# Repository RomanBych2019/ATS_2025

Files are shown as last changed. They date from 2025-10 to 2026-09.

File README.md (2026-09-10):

# ATS

Проект тарировочной станции на основе контроллера ESP32.
Дисплей на базе Nextion 5'.

# Основные возможности

Работа с ДУТами с интерфейсами:
- Аналоговый, напряжение
- Аналоговый, частота
- RS485, протокол LLS
- BLE фирмы Эскорт

Работа в режимах:
- Счетчик - подсчет топлива, прошедшего через счетчик. Запоминание промежуточных значений, управление насосом.
- Выдача топлива - выдача введенного объема топлива.
- Автоматическое выкачивание - выкачивание топлива из бака до тех пор, пока скорость потока не станет менее 5 л/мин.
- Калибровка счетчика - вычисление количества импульсов для калибровки счетчика.
- Тарировка бака - тарировка бака порциями топлива.

Станция передает данные в терминал спутникового мониторинга, подключенный по RS485 (19200, 8, 1), протокол передачи Modbus RTU.
Станция записывает лог работы во внутреннюю flash-память.

# Сборка

Проект собирается через PlatformIO. В `platformio.ini` есть два варианта прошивки:

- `esp32dev` - основная сборка без Web Portal и Wi-Fi.
- `esp32dev_web` - сборка с Web Portal, Wi-Fi и OTA через флаг `ENABLE_WEB_PORTAL`.

Команды сборки:

```sh
pio run -e esp32dev
pio run -e esp32dev_web
```

В обычной сборке `WebUi.cpp`, `WifiManager.cpp` и зависимость `GyverPortal` не используются. В web-сборке они подключаются на этапе выбора environment.

# Web Portal

Web Portal доступен только в сборке `esp32dev_web`.

Станция работает в режиме точки доступа:
- SSID: `WiFi ATS`
- Пароль: `00000001`

Страницы:
- `192.168.4.1` - управление станцией и доступ к логу.
- `192.168.4.1/ota_update` - загрузка новой прошивки.

# Структура

Крупные части логики вынесены из `main.cpp` в отдельные модули:
- `HmiRenderer` - рендеринг экранов Nextion.
- `WebUi` - страницы и обработчики Web Portal.
- `WifiManager` - настройка Wi-Fi и login portal.
- `ModbusTable` - таблица Modbus и обновление регистров.

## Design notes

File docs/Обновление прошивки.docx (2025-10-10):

1. Подключиться к Wi-Fi сети ATC, paswd: 12_04_19
2. Убедиться, что присвоен IP адрес из диапазона 192.168.4.ххх
3. Перейти в браузере по адресу 192.168.4.1/upgrade

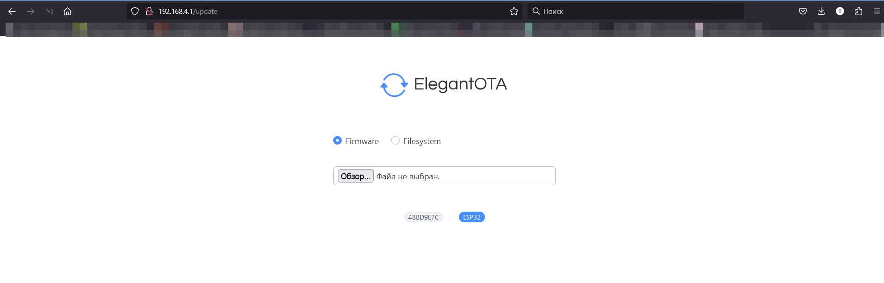
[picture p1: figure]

4. Выбрать файл для загрузки firmware.bin нажатием кнопки Обзор
5. Дождаться окончания загрузки

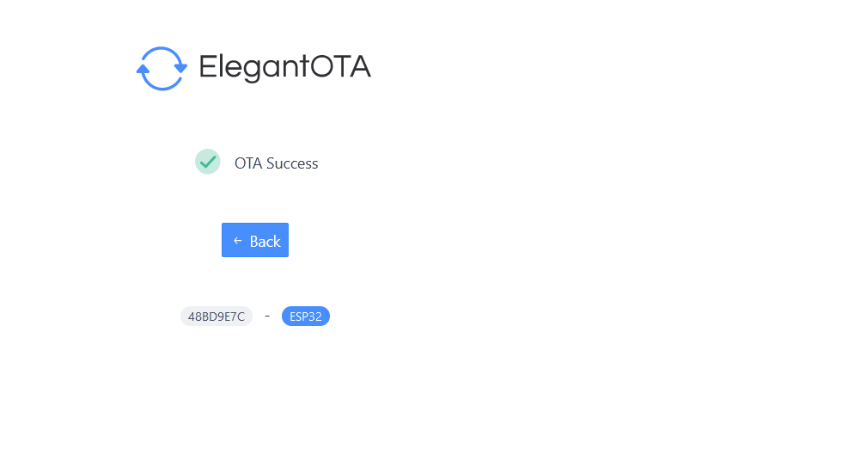
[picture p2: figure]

6. Все! Прошивка обновлена. Проверить можно вновь подключившись к Wi-Fi сети ATC и зайдя на адрес 192.168.4.1

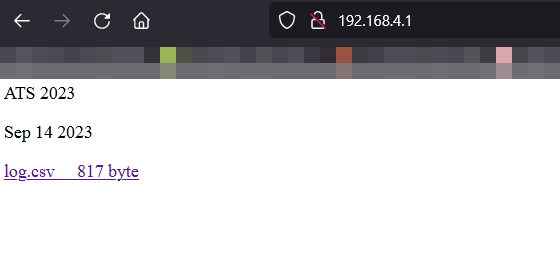
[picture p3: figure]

Скачав файл log.svc можно получить историю тарировок с датами начала, идентификатором и настройками каждой тарировки.

Удаление файла из памяти станции по ссылке http://192.168.4.1/delete

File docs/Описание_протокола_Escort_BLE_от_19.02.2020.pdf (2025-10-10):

2020

## УТВЕРЖДЕНО А.В.00001-01 33 01-ЛУ

## ПРОТОКОЛ ВЗАИМОДЕЙСТВИЯ УСТРОЙСТВ НА БЕСПРОВОДНОЙ ТЕХНОЛОГИИ С НИЗКИМ ЭЛЕКТРОПОТРЕБЛЕНИЕМ (ЭСКОРТ.BLE)

## Руководство программиста

А.В.00001-01 33 01

А.В.00001-01 33 01

## АННОТАЦИЯ

### В данном программном документе приведено руководство программиста по использованию протокола взаимодействия устройств на беспроводной технологии с

низким электропотреблением ЭСКОРТ.BLE.

В данном программном документе, в разделе «Термины, определения, обозначения и сокращения» описаны используемые в описании протокола термины,

### определения, обозначения и сокращения для однозначной трактовки в рамках данного

протокола.

### В разделе «Параметры соединения» приведено описание параметров необходимых для установления соединения между управляющим и оконечным

устройством.

### В данном программном документе, в разделе «Структура сообщения» приведено описание организации обмена данными между управляющим и оконечным

устройством.

### В разделе «Передаваемые параметры» описана структура используемых в организации обмена данными между управляющим и оконечным устройством

параметров и приведен список используемых параметров.

### В данном программном документе, в разделе «Используемые команды» приведено описание команд обеспечивающих выполнение тех или иных действий по

запросу от управляющего устройства оконечным устройством.

Оформление | программного | документа | «Руководство | программиста»

### произведено по требованиям ЕСПД (ГОСТ 19.101-7

### 1), ГОСТ 19.103-77²⁾, ГОСТ 19.104-

78*³⁾, ГОСТ 19.105-78*⁴⁾, ГОСТ 19.106-78*⁵⁾, ГОСТ 19.504-79*⁶⁾, ГОСТ 19.604-78*⁷⁾).

1) ГОСТ 19.101-77 ЕСПД. Виды программ и программных документов
2) ГОСТ 19.103-77 ЕСПД. Обозначение программ и программных документов
3) ГОСТ 19.104-78* ЕСПД. Основные надписи
4) ГОСТ 19.105-78* ЕСПД. Общие требования к программным документам
5) ГОСТ 19.106-78* ЕСПД. Общие требования к программным документам, выполненным печатным способом
6) ГОСТ 19.504-79* ЕСПД. Руководство программиста. Требования к содержанию и оформлению
7) ГОСТ 19.604-78* ЕСПД. Правила внесения изменений в программные документы, выполненные печатным способом

### Оглавление

3.1. РЕЖИМ НЕПОСРЕДСТВЕННОГО СОЕДИНЕНИЯ С СЕРВИСОМ УСТРОЙСТВА........7
4.1. РЕЖИМ НЕПОСРЕДСТВЕННОГО СОЕДИНЕНИЯ С СЕРВИСОМ УСТРОЙСТВА........8

### 1. ТЕРМИНЫ, ОПРЕДЕЛЕНИЯ, ОБОЗНАЧЕНИЯ И СОКРАЩЕНИЯ

В данном протоколе применены следующие термины с соответствующими определениями:

* | Управляющее устройство — устройство осуществляющее формирование команд управления (в дальнейшем запросов) и прием ответных команд (в дальнейшем ответов).
* | Оконечное устройство — устройство преобразующее физические воздействия в параметры и отвечающее на команды управления.
* | Команда — набор букв, означающий необходимость выполнения того или иного действия.
* | Параметр команды — конструкция, позволяющая идентифицировать и передать некоторое значение.
* | Разделитель полей — символ, разделяющий команды и параметры.
* | Разделитель параметра — символ, отделяющий элементы параметра.
* | Исходящие параметры — параметры, передаваемые из управляющего устройства в оконечное.
* | Входящие параметры — параметры, передаваемые из оконечного устройства в управляющее.
* | Характеристика (Characteristic) — это значение передаваемых данных, используемое в сервисе, а также информация конфигурации о том, как осуществляется доступ к этому значению, и информация о том, как это значение отображается.
* | Сервис (Service) — это набор характеристик, сервис представляет собой набор данных и связанных с ними действий для выполнения определенной функции или задачи.
* | Универсальный уникальный идентификатор (Universally Unique ID) - это уникальный номер, используемый для идентификации служб, характеристик и дескрипторов, также называемых атрибутами.
* | Advertising — процесс широковещательной трансляции пакетов оконечным BLE устройством. В этих пакетах оконечное устройство сообщает своё имя и адрес, сообщает о сервисах, которые предоставляет, а также специальную информацию.
* | Manufacturer specific data – поле в advertising сообщении, в котором широковещательно передаются измеряемые параметры оконечным устройством.

В данном протоколе применены следующие обозначения и сокращения:

UUID - (Universally Unique ID) Универсальный уникальный идентификатор;
BLE - (Bluetooth Low Energy) технология Bluetooth c низким энергопотреблением.

### 2. ПАРАМЕТРЫ СОЕДИНЕНИЯ

На физическом уровне соединение с оконечным устройством реализовано на основе стандарта Bluetooth 4.0 со следующими параметрами соединения :
Параметр | Значение
advertising_interval | 1000 мс
connection_interval | 900 мс
slave_latency | 1
conn_sup_timeout | 5000 мс

Оконечные устройства имеют уникальное имя в формате TD_XXXXXX –для топливного датчика , TL_XXXXXX-для датчика температуры и освещенности , TT_XXXXXX- для датчика температуры ,TH_XXXXXX- для датчика температуры влажности ,давления и освещенности , DU_XXXXXX для датчика угла наклона , где XXXXXX - представляет собой серийный номер оконечного устройства.
С оконечными устройствами можно взаимодействовать двумя способами: при помощи непосредственного соединения с устройством и обменом данными при помощи характеристик Rx characteristics и Tx characteristics UUID (двухсторонний обмен – наиболее подходит для начальной
настройки | (калибровки) устройства), | либо при | помощи | advertising | (рекламных | либо
широковещательных) пакетов, что обеспечивает лишь односторонний обмен с оконечным устройством – получение телеметрических данных измеряемых оконечным устройством.
Оба этих режима работают независимо, то есть при установлении непосредственного соединения с каким-либо управляющим устройством оконечное устройство не перестает рассылать advertising сообщения.

### 2.1. Режим непосредственного соединения (рекомендуется для конфигурации оконечного

устройства)

Обмен происходит при помощи BLE -сервиса включающего две характеристики:

2.1.1. Service UUID: 6E400001-B5A3-F393-E0A9-XXXXXXXXXXXX (little endian) - идентификатор сервиса при помощи которого осуществляется обмен данными между управляющим и оконечным устройством.
Передача данных от управляющего к оконечному устройству осуществляется путем записи в идентификатор характеристики для передачи данных управляющим устройством (Tx characteristics UUID).
Прием данных от оконечного устройства осуществляется путем считывания идентификатора характеристики для приема данных управляющим устройством (Rx characteristics UUID)
2.1.2. Rx characteristics UUID: 6E400003-B5A3-F393-E0A9-XXXXXXXXXXXX (little endian) -идентификатор характеристики для приёма данных управляющим устройством.
2.1.3. Tx characteristics UUID: 6E400002-B5A3-F393-E0A9-XXXXXXXXXXXX (little endian) -идентификатор характеристики для передачи данных управляющим устройством.

Примечание:
XXXXXXXXXXXX это уникальная часть UUID для каждой пары (управляющее-оконечное) устройство.

### 2.2. Режим связи через advertising (широковещательные) пакеты

Оконечное устройство отсылает через равные промежутки времени (1000 ms) advertising пакеты и передает в поле manufacturer specific data данные телеметрии уникальные для каждого типа оконечного устройства.
В режиме когда к датчику нет непосредственного соединения, advertising ведется в режиме Connectable undirected (ненаправленное, с возможностью соединения). При наличии соединения с сервисом оконечного устройства (непосредственное соединение) advertising ведется в режиме Non connectable undirected (ненаправленное без возможности соединения).

Пример пакетов advertising:
1. Non connectable undirected (ненаправленное, без возможности соединения) 0x0201060FFF160F01B50B1D1875CF1D000000800A0954445F313030303032.
2. Connectable undirected (ненаправленное, с возможностью соединения) 0x0201060FFF160F01B50B1D1875CF1D000000800A0954445F3130303030321107A286C1DDEEFFA9 E093F3A3B50100406E.

Разбор advertising пакета:
1. 020106
Длина = 0x02, Тип 0x01 = «Flags»
Данные = 06, что соответствует BLE_GAP_ADV_FLAG_LE_GENERAL_DISC_MODE BLE_GAP_ADV_FLAG_BR_EDR_NOT_SUPPORTED
2. 0FFF160F01CF0B1D1775CF1D00000080
Длина = 0x0F, Тип 0xFF = «Manufacturer data»
Данные = 160F01CF0B1D1775CF1D00000080 - это полезные данные, предаваемые датчиком, разбор и формат этих данных приведен в параграфе 3. СТРУКТУРА СООБЩЕНИЯ и 4.ПЕРЕДАВАЕМЫЕ ПАРАМЕТРЫ
3. 0A0954445F313030303032
Длина = 0x0A, Тип 0x09 = «Complete Local Name» (имя устройства) Данные = 54445F313030303032 =TD_100002 (hex –ascii)
4. 1107A286C1DDEEFFA9E093F3A3B50100406E
Длина = 0x11, Тип 0x07 = «Complete List of 128-bit Service Class UUIDs» Данные = A286C1DDEEFFA9E093F3A3B50100406E

### 3. СТРУКТУРА СООБЩЕНИЯ

### 3.1. Режим непосредственного соединения с сервисом устройства

В режиме непосредственного соединения все сообщения передаются в виде следующей структуры:

Тип поля | Пример
Команда / Ответ на команду | Например, SP –установить пароль Ответом на команду будет (в случае успеха) APO или APE (в случае неудачи) Подробнее о командах в параграфе 5.
разделитель полей | запятая
параметр1 | PW:1:123456 –старый пароль , необходим для установки нового Подробнее о параметрах в параграфе 4.
разделитель полей | запятая
параметр2 (если необходимо) | PN:1:5555 –новый пароль. Подробнее о параметрах в параграфе 4.
разделитель полей | запятая
конец сообщения | символ конца строки (\r)

Итоговое сообщение:

SP,PW:1:123456,PN:1:5555\r –установить новый пароль 5555, при условии что старый пароль был 123456.

Примечания:
1. Сообщение может быть без параметров. В этом случае разделители полей отсутствуют.
2. Количество параметров в сообщении может быть произвольным (рекомендуется не более 20).

### 3.2. Поле manufacturer data в advertising сообщении

Все параметры передаются в поле manufacturer data и имеют фиксированный размер в байтах. Первые два байта в поле manufacturer data задают параметр company id.
Следующий байт задает параметр hardware id –тип устройства с которым ведется работа
В зависимости от hardware id изменяется формат дальнейших данных, который является уникальным для каждого типа устройств.
Формат передаваемых данных и пример посылок приведен в параграфе 4.2 ПЕРЕДАВАЕМЫЕ ПАРАМЕТРЫ.

### 4. ПЕРЕДАВАЕМЫЕ ПАРАМЕТРЫ

### 4.1. Режим непосредственного соединения с сервисом устройства

4.1.1. Структура передаваемого параметра

Передаваемый параметр представляет собой конструкцию ИМЯ: ТИП: ЗНАЧЕНИЕ.

ИМЯ –символьное название параметра. (см. табл.1, табл.2, табл.3)
РАЗДЕЛИТЕЛЬ ПАРАМЕТРА — двоеточие.
ТИП – тип передаваемого параметра,
0 - ЧИСЛО ШЕСТНАДЦАТЕРИЧНОГО ФОРМАТА (HEX) ЗАПИСАННОЕ В КОДЕ ASCII
1 – ЦЕЛОЧИСЛЕННЫЙ (РЕКОМЕНДУЕТСЯ ИСПОЛЬЗОВАТЬ INT_16)
2 – С ПЛАВАЮЩЕЙ ТОЧКОЙ (РЕКОМЕНДУЕТСЯ FLOAT),
3 – СТРОКОВЫЙ (ПРОИЗВОЛЬНАЯ СТРОКА - РЕКОМЕНДУЕТСЯ НЕ БОЛЕЕ 12 СИМВОЛОВ) РАЗДЕЛИТЕЛЬ ПАРАМЕТРА — двоеточие.
ЗНАЧЕНИЕ – значение в зависимости от типа.

Пример ответа на команду GD\r «Выдать динамические параметры»: AGD,UT:1:-20,UL:1:1024,VB:2:3.62,ER:3:overcool\r

Входящие параметры в строке:
* | Температура = -20 град.
* | Уровень = 1024 у.е.
* | Напряжение батареи = 3,62 В.
* | За время между сеансами связи оконечного устройства с управляющим произошла ошибка overcool— переохлаждение.

Примечания:

1. Количество передаваемых параметров определяется разработчиком прибора в зависимости от его специфики и режима работы. Количество параметров в сообщении может быть произвольным (рекомендуется не более 20) при указанных рекомендуемых параметрах размер буфера на приеме и передаче не должен превышать 512 байт.
2. Если не указано иного тип параметра считать целочисленным.
3. Опционально при выполнении запроса могут быть добавлены параметры вида N1, N2, N3…….
4. Порядок следования параметров может быть произвольным, некоторые параметры могут отсутствовать.

4.1.2. Список рекомендуемых динамических параметров приведен в таблице 1. Таблица 1. Список рекомендуемых динамических параметров
Параметр | Величина | Примечание
UT | Значение температуры | В градусах Цельсия
UL | Значение уровня для топливного датчика (событие сработки для датчика угла) | В диапазоне 0...4095 или 0..1023 в зависимости от режима для топливного датчика В диапазоне от 0..2 для датчика угла
UM | Значение уровня | В мм.
UZ | Накопленный измеренный расход | В литрах ***
UC | Счетчик событий (импульсов) | В событиях***
US | Измеренный период сигнала | В ms
UV | Измеренное напряжение | В вольтах
UI | Измеренный ток | В амперах
UF | Измеренная частота | В Гц.
UP | Измеренное давление | В паскалях
UM | Измеренный вес | В кг.
UN | Угол наклона | в градусах
UA | Азимут | В градусах
QV | Уровень вибрации (качество вождения) | В баллах больше-хуже
DC | Битовая маска сухого контакта | Не более 15 контактов.
VB | Напряжение питания (батареи)
ER | Ошибка, возникшая в процессе работы
TO | Время включения (в режиме отвал) ,Время накопления данных угла (в режиме ковш) | В секундах , не более 200 секунд
TF | Время выключения(в режиме отвал и ковш) | В секундах , не более 200 секунд

Примечание:
*** Счетчик. Сбрасывается соответствующей командой сброса

4.1.3. Список рекомендуемых калибровочных параметров приведен в таблице 2.

Таблица 2. Список рекомендуемых калибровочных параметров

HK | Верхнее калибровочное значение параметра
LK | Нижнее калибровочное значение параметра
AK | Зафиксировать горизонтальное положение
AС | Значение коэффициента 2 порядка при аппроксимации параметра
AB | Значение коэффициента 1 порядка при аппроксимации параметра
AА | Значение постоянной составляющей при аппроксимации параметра
AD | Значение коэффициента 3 порядка при аппроксимации параметра
PW | Пароль на смену калибровочных значений
PN | Новый пароль при смене пароля
WM | Режим работы | Определяется разработчиком.
UD | UUID
4.1.4. Список рекомендуемых статических параметров приведен в таблице 3.

Таблица 3. Список рекомендуемых статических параметров

SE | Серийный номер прибора.
VV | Версия прошивки
VD | Тип устройства.
CR | Контрольная сумма прошивки. | CRC32 вычисляется в момент формирования значения параметра.
FP | Ввод заводского пароля. | Для программирования параметров исключительно в процессе производства.

### 4.2. Поле manufacturer data в advertising сообщении

Общая структура поля Manufacturer data в advertising сообщении (справедлива для всех типов оконечных устройств).

Номер байта | 0 | 1 | 2 | 3 | 4 и далее
Значение | Длина поля | Тип поля (Manufacturer data) | Company ID | Hardware id (тип устройства) | Полезные данные (параметры датчика)
Пример | 0x0F | Всегда 0xFF | 0x0F16 | 0x01- ДУТ | 0xCF0B1D1775CF1D00000080

Для того чтобы различать типы устройств был введен байт hardware id -тип устройства, список устройств приведен ниже. Байт hardware id определяет набор полезных параметров получаемых от оконечного устройства их размер и порядок следования.

Байт hardware id | Тип устройства
0x01 | Датчик уровня топлива (ДУТ)
0x02 | Температурный датчик
0x03 | Температурный датчик c измерением уровня освещенности
0x04 | Датчик угла
0x05 | Датчик температуры, влажности, освещённости и давления

Список устройств может быть расширен.
Ниже приводится формат посылки полезных параметров для каждого из типов устройств.

Датчик уровня топлива (ДУТ), 0x01 - тип устройства. Имя вида TD_XXXXXX ,где XXXXXX соответствует серийному номеру.

Номер по порядку | Тип параметра | Длина параметра (байт) | Диапазон | Единица измерения | Пример
1 | Уровень топлива | 2 | 0...1023 или 0…4095 | Условные единицы | 2C0C - уровень (обратный порядок байт) 0с2с (hex) = 3116 (dec)
2 | Напряжение встроенной батареи | 1 | 2..4 | Вольт*10 | 1D - напряжение батареи *10 = 29 (dec)= 2.9 вольта
3 | Температура | 1 | -70..125 | Градус Цельсия | 17- темпрература = 23 (dec) градуса
4 | Версия прошивки | 1 | 0..255 | Номер версии | 74 -версия прошивки = 116 (dec)
5 | Период (непосредствен но измеренный параметр) | 4 | 0..500000 | Условные единицы | CF1D0000 (обратный порядок байт) =00001DCF(hex)= 7631(dec)
6 | Режим работы (определяет в каком диапазоне | 1 | Два значения: 0x80- 4095 0x00 -1024 | Нет | Если установлен диапазон 4095, байт принимает значение 0x80 , если 1024 ,то 0x00

| работает датчик)
7 | Сглаживание (младший полубайт) + Термокомпенса ция(старший полубайт) | 1 | Сглаживание : 0x0..0xF (0..15) Термокомпенса ция: Два значения: 0x8-выключена 0x0 -включена | Условные единицы | 0x81 Термокомпенсация выключена , Сглаживание=0x1(hex)= 1(dec) 0x0F Термокомпенсация включена , Сглаживание=0xF(hex)= 15(dec)

Температурный датчик ,0x02 - тип устройства. Имя вида TT_XXXXXX ,где XXXXXX соответствует серийному номеру.

Номер по порядку | Тип параметра | Длина параметра (байт) | Диапазон | Единица измерения | Пример
1 | Температура | 2 | -700..1250 | Градус Цельсия*10 | 6E01 - температура*10 (обратный порядок байт) - 016E (hex) = 366 (dec) =36.6 градусов
2 | Напряжение встроенной батареи | 1 | 2..4 | Вольт*10 | 1D - напряжение батареи *10 = 29 (dec)= 2.9 вольта
3 | Версия прошивки | 1 | 0..255 | Номер версии | 7C -версия прошивки = 124 (dec)

Температурный датчик c измерением уровня освещенности ,0x03 - тип устройства. Имя вида TL_XXXXXX, где XXXXXX соответствует серийному номеру.

Номер по порядку | Тип параметра | Длина параметра (байт) | Диапазон | Единица измерения | Пример
1 | Температура | 2 | -700...1250 | Градус Цельсия*10 | 6E01 - температура*10 (обратный порядок байт) - 016E (hex) = 366 (dec) =36.6 градусов
2 | Освещённость | 2 | 0...10000 | Люкс | Освещенность (обратный порядок байт) - 0с2с (hex) = 3116 (dec) =3116 люкс
3 | Напряжение встроенной батареи | 1 | 2...4 | Вольт*10 | 1D - напряжение батареи *10 = 29 (dec)= 2.9 вольта

4 | Версия
прошивки
1 | 0...255 | Номер версии

7D -версия прошивки =
125 (dec)

Датчик угла,0x04 - тип устройства . Имя устройства вида DU_XXXXXX ,где XXXXXX соответствует серийному номеру.

Номер по порядку | Тип параметра | Длина параметра (байт) | Диапазон | Единица измерения | Пример
1 | Режим датчика угла | 1 | 0,4,5,6,9,10 | Режим, подробнее в паспорте на DU-BLE , и в руководстве | 0x06=Режим 6= Включен режим датчика угла
2 | Событие сработки | 1 | 0..2 | Событие сработки подробнее в паспорте на DU-BLE , и в руководстве | В режиме 6 : 0x01-произошло событие сработки- угол превышен
3 | Угол наклона | 2 | 0..180 | Градус | 0x0300 (little endian)-обратный порядок байт =3(dec) градуса
4 | Температура | 1 | -70...125 | Градус Цельсия | 0x17(hex)- температура = 23 (dec) градуса , параметр не используется в 102 версии прошивки , передается всегда 0x00
5 | Верхняя калибровка угла | 2 | 0...180 | Градус, подробнее в паспорте на DU-BLE , и в руководстве | 0x0096 (big endian) =225 (dec) градусов
6 | Нижняя калибровка угла | 2 | 0...180 | Градус, подробнее в паспорте на DU-BLE , и в руководстве | 0x0005 (big endian) =5 (dec) градусов

7 | Напряжение встроенной батареи | 1 | 2...4 | Вольт*10 | 0x1D(hex) - напряжение батареи *10 = 29 (dec)= 2.9 вольта
8 | Версия прошивки | 1 | 0...255 | Номер версии | 0x66(hex) -версия прошивки = 102 (dec)

Датчик температуры, влажности, освещённости и давления,0x05 - тип устройства. Имя вида TH_XXXXXX ,где XXXXXX соответствует серийному номеру.

Номер по порядку | Тип параметра | Длина параметра (байт) | Диапазон | Единица измерения | Пример
1 | Температура | 2 | -700...1250 | Градус Цельсия*10 | 0x6E01 (hex) little endian(обратный порядок байт) – 0x016E (hex) = 366 (dec) =36.6 градусов
2 | Освещённость | 2 | 0...10000 | Люкс | 0x2C0C (hex) little endian (обратный порядок байт) - 0с2с (hex) = 3116 (dec) =3116 люкс
3 | Влажность | 2 | 0..1000 | %*10 | 0x2b02=little endian (обратный порядок байт) =0x022b (hex)=55.5% влажности
4 | Атмосферное давление | 2 | 8000..11000 | Па/10 | 0x9427=little endian(обратный порядок байт) =0x2794(hex) =10132(dec)=101320 Па
5 | Напряжение встроенной батареи | 1 | 2...4 | Вольт*10 | 1D - напряжение батареи *10 = 29 (dec)= 2.9 вольта
6 | Версия прошивки | 1 | 0...255 | Номер версии | 7D -версия прошивки = 125 (dec)

### 5. ИСПОЛЬЗУЕМЫЕ КОМАНДЫ

Только для режима непосредственного соединения с сервисом устройства

В таблице 4 приведен список используемых команд, с описанием действия выполняемого по команде, исходящих и входящих параметров.

Таблица 4. Список основных команд.

Действие | Запрос | Исходящие параметры, рекомендуемые для запроса | Ответ | Входящие параметры, рекомендуемы е для ответа | Примечание
Перезагрузка | PR | PW-пароль** | APR | -
Уход в сон | PS | PW-пароль** | APS | - | Уход в глубокий сон внешним магнитным воздействием (при помощи магнита)
Директивная установка калибровочны х параметров | SD | PW-пароль**+ Любой из калибровочных параметров, возможна комбинация из нескольких параметров из Табл.3* | ADO-ADE | - ADO-если параметры | установлены успешно. ADE-если не удалось по каким-либо причинам установить параметр.
Калибровка верхнего уровня | SH | PW-пароль** | ASH | HK-значение на момент калибровки | В зависимости от устройства
Калибровка нижнего уровня | SL | PW-пароль** | ASL | LK-значение на момент калибровки | В зависимости от устройства
Калибровка горизонта | SA | PW-пароль** | ASA
Установка времени включения/вы ключения | ST | PW-пароль** | ATO-ATE | TO-время включения TF-время выключения Подробнее в паспорте и руководстве пользователя датчика угла | ATO-если параметры установлены успешно. ATE-если не удалось по каким-либо причинам установить параметр.
Установка нового пароля | SP | PW-пароль** или FP- заводской пароль+ PN- новый пароль | APO-APE | - APO -если успешно | APE -если не успешно
Сброс накопленных | SC | PW-пароль** | ASC | -

значений счетчиков

Установка режима | SW | PW-пароль** | AWO-AWE | WM-режим работы | AWO -если успешно установлен AWE -если не установлен
Установка времени задержки | ST | PW-пароль** | ATO-ATE | TM-время задержки,секун д | ATO -если успешно установлено ATE -если не установлено
Запрос динамических параметров | GD | - | AGD | Параметры из Табл.1 *
Запрос всех параметров | GA | - | AGA | Параметры из Табл.1, Табл.2, Табл.3*
При выполнении команды на которую нет доступа | - | - | WRN | - | Имеется ввиду, что не вводился пароль на одну команду или был введен неверно, неизвестная команда или параметр.

Примечания:
* Количество параметров по усмотрению разработчика или в соответствии с установленным режимом
** Если пароль равен 0 передача параметра PW не требуется.

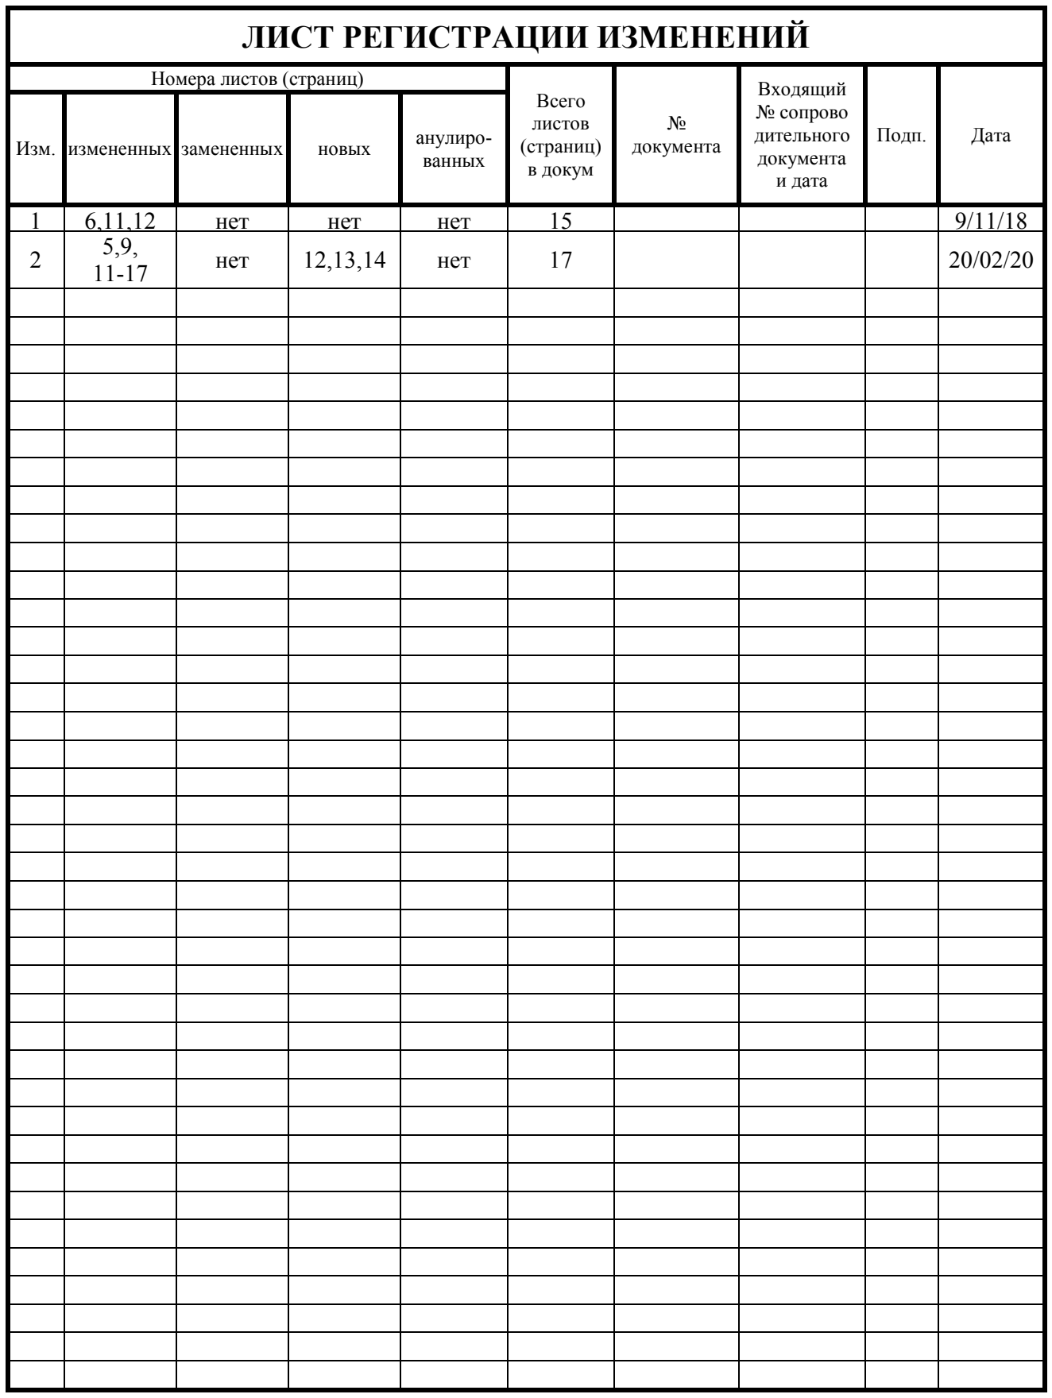
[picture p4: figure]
ЛИСТ РЕГИСТРАЦИИ ИЗМЕНЕНИЙ; Номера листов (страниц); Всего листов (страниц) в докум; № документа; Входящий № сопрово дительного документа и дата; Подп.; Дата; нет

Изм. | измененных | замененных | новых | анулиро-ванных
2 | 5,9, 11-17 | нет | 12,13,14 | нет | 17 | 20/02/20

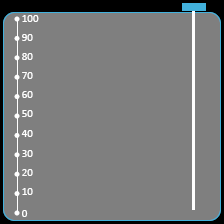
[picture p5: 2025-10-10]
display/Бак2.bmp

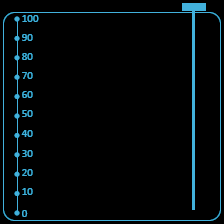
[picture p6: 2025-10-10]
display/Бак.bmp

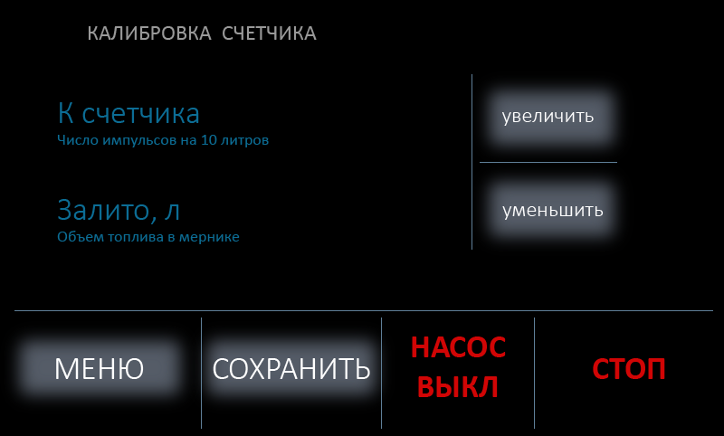
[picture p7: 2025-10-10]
display/Экран 5'_ver2.bmp

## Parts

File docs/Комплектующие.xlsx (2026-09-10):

№ | Наименование | Производитель, продавец | Срок поставки | Кол-во в изделии | Минимальный заказ | Цена | Стоимость
Блок управления
 | Печатная плата | Резонит | 30 дней | 1 | 5 |  |  | в наличии
 | Разъем microFit 2X8 вилка на плату вертикальная |  |  | 1
 | Разъем microFit 2X8 розетка | https://www.chipdip.ru/product/430251610-40-c-125-c-3mm-2x8p-micro-fit-mx-3.0-8-2-molex-8037730066 |  | 1
 | Микроконтроллер ESP32 30pin | https://aliexpress.ru/item/1005009623884970.html?shpMethod=CAINIAO_ECONOMY&sku_id=12000049665783738 |  | 1 |  | 308
 | Ключ IRF7311PBF | https://www.chipdip.ru/product/irf7311tr-tranzistor-2n-mosfet-30v-9a-1.6vt-sop-8-umw-9001633824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 |  | 1 |  | 130
 | Модуль часов DS3231 | https://aliexpress.ru/item/1005009014018647.html?shpMethod=CAINIAO_SUPER_ECONOMY&sku_id=12000047581122284 |  | 1 |  | 112
 | АЦП ADS1115 | https://aliexpress.ru/item/1005009391101280.html?shpMethod=CAINIAO_SUPER_ECONOMY&sku_id=12000048955886588 |  | 1 |  | 172
 | DC12-DC5 | https://aliexpress.ru/item/4000510235449.html?sku_id=10000002487180986 |  | 1 |  | 250
 | Модуль RS485-TTL | https://aliexpress.ru/item/32705625990.html?sku_id=60857330082 |  | 2 |  | 146
 | Резисторы, конденсаторы
 | Стойки пластиковые, 10 мм. Отверстие D3 mm |  |  | 4
 | Винты M3, 6 мм |  |  | 8
 | Выключатель, 20 мм | https://www.ozon.ru/product/vyklyuchatel-kruglyy-klavishnyy-chernyy-6a250v-diametr-20mm-2-shtuki-893071984/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 |  | 1
 | Держатель предохранителя | https://www.ozon.ru/product/derzhatel-predohranitelya-5x20-10a-250v-dvp4-2-komplekt-2sht-3352411520/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 |  | 1
 | Разъем MIC4 16 (комплект) | https://www.vseinstrumenti.ru/product/razem-mic16-4p-gnezdo-pro-legend-metall-na-kabel-pl2202-6531865/ |  | 1 |  | 280
 |  | https://www.vseinstrumenti.ru/product/razem-mic16-4p-shteker-pro-legend-metall-na-korpus-pl2208-6532009/ |  | 1 |  | 200
 | Разъем MIC5 16 (комплект) | https://www.ozon.ru/product/razem-mic16-5-pin-shteker-gnezdo-metall-1275774743/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 |  | 2
 |  | https://www.ozon.ru/product/razem-mic16-5-pin-shteker-gnezdo-metall-1275774743/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 |  | 2 |  | 230
 | Дисплей NX8048P050 011R Y | https://aliexpress.ru/item/1005005311087521.html?shpMethod=CAINIAO_STANDARD_HEAVY&sku_id=12000032584294398 |  | 1 |  | 6182
 | Корпус G317 | https://www.chipdip.ru/product/g317 |  | 1 |  | 1160
Блок силовой
 | Корпус 12 мест, выносной | https://www.vseinstrumenti.ru/product/boks-iek-schrn-p-12-iek-mkp12-n-12-40-10-1114226/ |  | 1 |  | 1200
 | Блок питания AC220/DC12 | https://www.vseinstrumenti.ru/product/stabilizirovannyj-blok-pitaniya-istochnik-davikon-ivep-1230-din-din-12v-3a-ivep-1230din-1791775/ |  | 1 |  | 1031
 | Автомат 10А | https://www.vseinstrumenti.ru/product/avtomaticheskij-vyklyuchatel-ekf-averes-av-10-1p-10a-10ka-sqmcb10-1-10b-av-1379455/ |  | 1 |  | 670
 | Лампа индикаторная 220В | https://www.vseinstrumenti.ru/product/indikator-chint-nd9-1-r-krasnyj-ac-dc-230v-led-594113-1805645/ |  | 1 |  | 461
 | Реле 12В. 16А | https://www.vseinstrumenti.ru/product/promezhutochnoe-rele-f-f-pk-2p-un12v-ea06-001-006-1297576/ |  | 1
 | Кнопка включения | https://www.vseinstrumenti.ru/product/modulnaya-knopka-upravleniya-iek-kmu11-iek-mbd10-11-k51-1329830/ |  | 1 |  | 1421
 | Клеймы |  |  | 10

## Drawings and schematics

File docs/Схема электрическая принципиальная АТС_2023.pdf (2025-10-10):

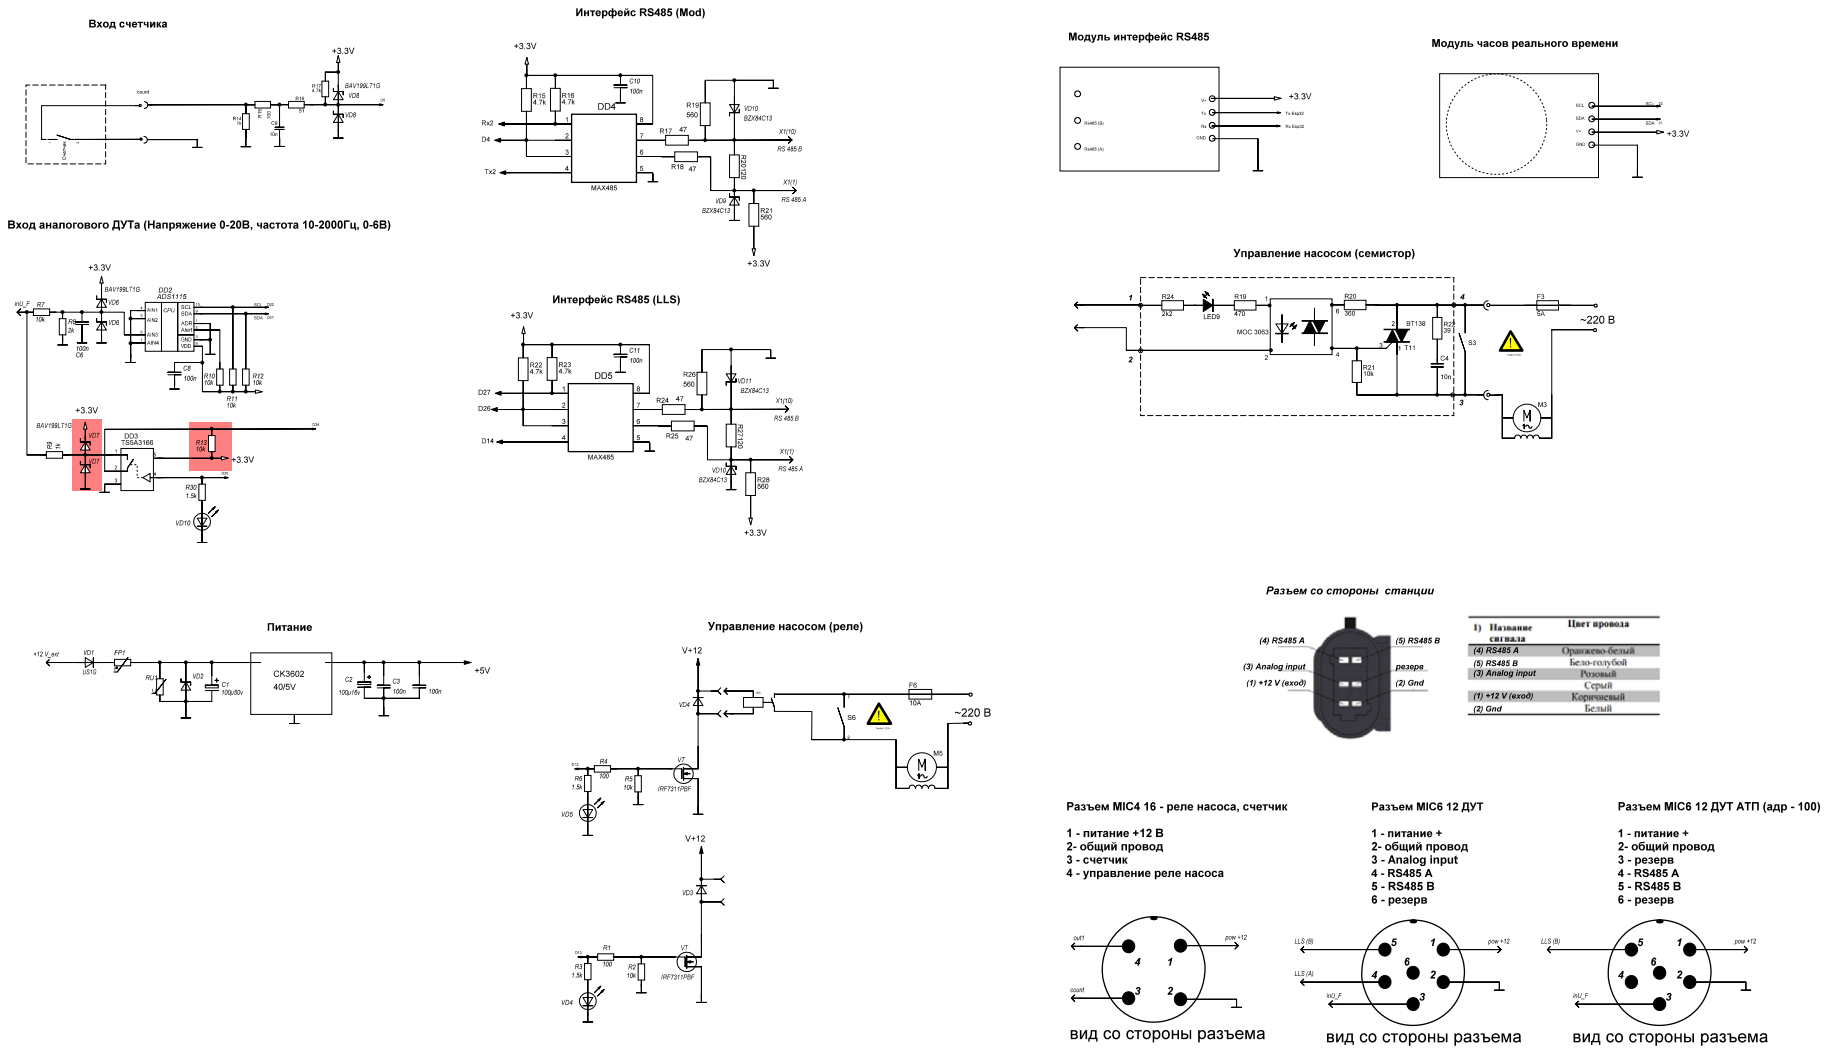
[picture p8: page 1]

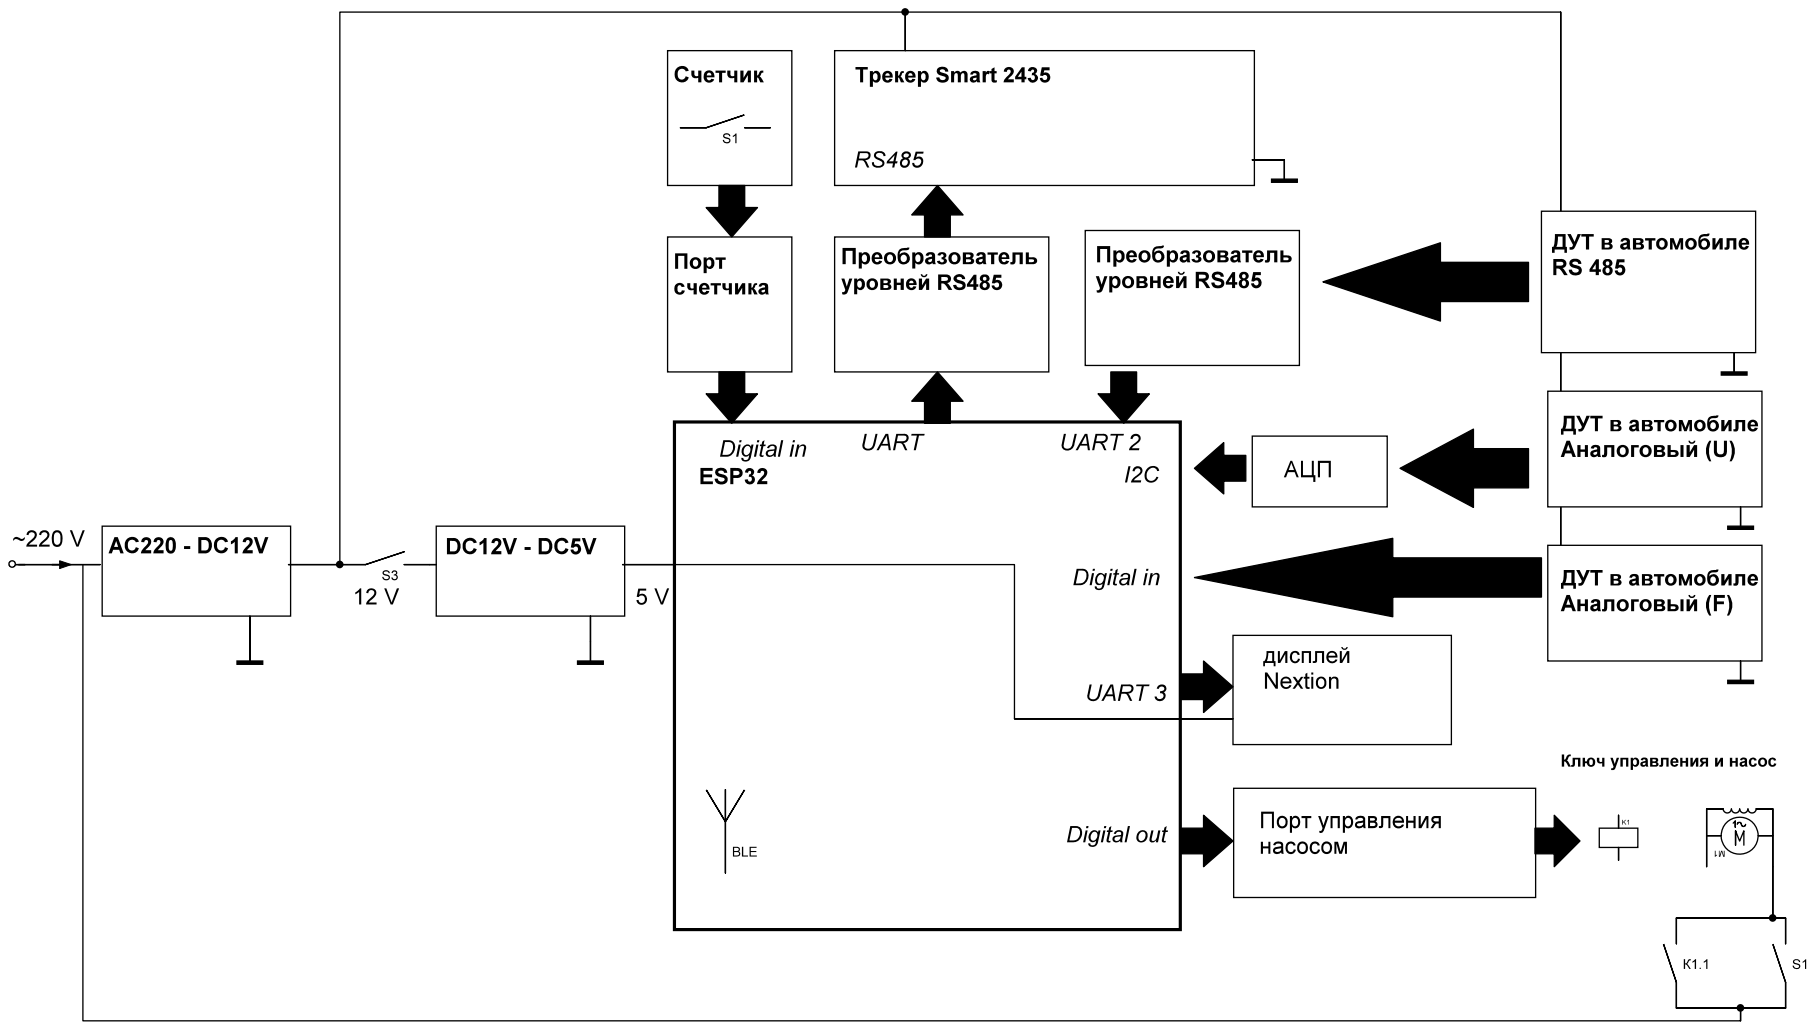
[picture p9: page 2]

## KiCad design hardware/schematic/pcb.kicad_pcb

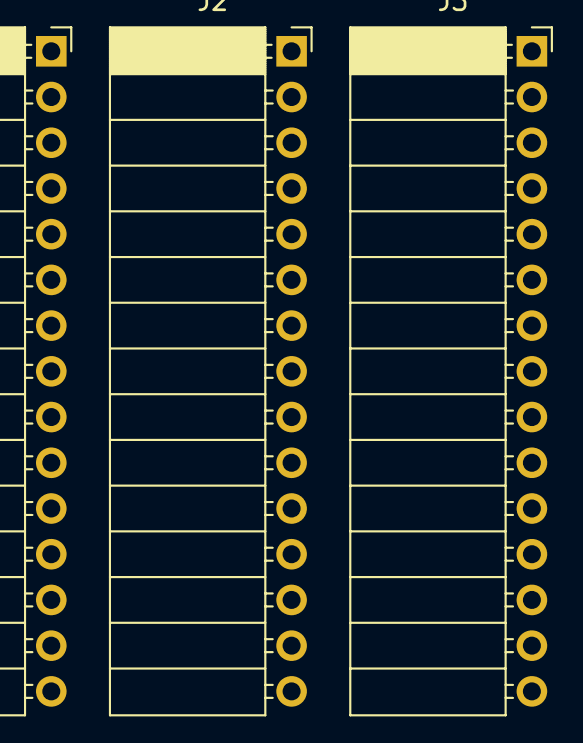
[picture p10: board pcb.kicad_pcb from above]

Board: 2 copper layers, 3 parts (0 on the bottom side), 10 nets, no tracks yet.

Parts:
J1: L; PinSocket_1x15_P2.54mm_Horizontal
J2: R; PinSocket_1x15_P2.54mm_Horizontal
J3: IR; PinSocket_1x15_P2.54mm_Horizontal

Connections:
unnamed: J1.12 (5V), J3.11 (VCC)
unnamed: J1.10 (A6), J3.10 (D8)
unnamed: J2.11 (D2), J3.3 (D1)
unnamed: J2.9 (D4), J3.4 (D2)
unnamed: J2.6 (D7), J3.5 (D3)
unnamed: J2.5 (D8), J3.6 (D4)
unnamed: J2.3 (D10), J3.7 (D5)
unnamed: J2.2 (D11), J3.8 (D6)
unnamed: J2.1 (D12), J3.9 (D7)
unnamed: J2.12 (GND), J3.1 (GND)

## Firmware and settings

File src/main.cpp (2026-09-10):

#include "main.h"
#ifdef verAnalogInput
#include "LS_ANALOG_U.h"
#include "LS_ANALOG_F.h"
#endif
#include "LS_RS485.h"
#include "LS_BLE.h"
#include "LS_EMPTY.h"
#include "HmiRenderer.h"
#include "ModbusTable.h"
#ifdef ENABLE_WEB_PORTAL
#include "WebUi.h"
#include "WifiManager.h"
#endif
// #include <TimeUtil.h>

const char *ssid = "WiFi ATS";
const char *password = "00000001";
#ifdef ENABLE_WEB_PORTAL
const char *VER = "2025_3.0 web 2.0";
#else
const char *VER = "2025_3.0";
#endif

LoginPass lp;
String errorStringWeb {};
int counter_display_resetring = 0;
volatile unsigned time_counter_imp = 0;

unsigned long start_pause, worktime, time_start_refill, time_LLS_update, time_stop_flow_rate;
bool autostop = false;
bool flag_HMI_send = false;
bool flag_conect_ok = true;

#ifdef ENABLE_WEB_PORTAL
WebData web_data;
#endif

const char *LOG_FILE_NAME = "log.csv";

hw_timer_t *My_timer = NULL;
RtcDS3231<TwoWire> Rtc(Wire);
Preferences flash;
EspSoftwareSerial::UART serialHMI;
#ifdef ENABLE_WEB_PORTAL
GyverPortal ui(&LittleFS);
#endif

ILEVEL_SENSOR *lls;
LS_RS485 *lls_RS485;
LS_BLE *lls_Ble;
LS_EMPTY *lls_Empty;
#ifdef verAnalogInput
Adafruit_ADS1115 ads;
LS_ANALOG_F *lls_analog_f;
LS_ANALOG_U *lls_analog_u;
#endif

#ifdef verATP
LS_RS485 *lls_ATP;
#endif

Out *pump;
Out *out_tmp;
COUNTER *countV;
TANK *tank;
TARRING *tar;
NEXTION hmi(serialHMI);

static volatile bool countIndicatorTimerActive = false;

static void setupCountIndicatorTimer()
{
#if ESP_ARDUINO_VERSION_MAJOR >= 3
    My_timer = timerBegin(1000000);
    timerAttachInterrupt(My_timer, &onTimer);
#else
    My_timer = timerBegin(0, 80, true);
    timerAttachInterrupt(My_timer, &onTimer, true);
    timerAlarmWrite(My_timer, 1000000, false);
#endif
}

static bool isCountIndicatorTimerActive()
{
#if ESP_ARDUINO_VERSION_MAJOR >= 3
    return countIndicatorTimerActive;
#else
    return timerAlarmEnabled(My_timer);
#endif
}

static void startCountIndicatorTimer()
{
    countIndicatorTimerActive = true;
#if ESP_ARDUINO_VERSION_MAJOR >= 3
    timerWrite(My_timer, 0);
    timerAlarm(My_timer, 1000000, false, 0);
#else
    timerAlarmEnable(My_timer);
#endif
}

void setup()
{
    pinMode(GPIO_NUM_2, OUTPUT);
    pinMode(INDI_F_PIN_, OUTPUT);
    pinMode(INIDICATE_COUNT, OUTPUT);

    // индикация начала загрузки
    digitalWrite(INDI_F_PIN_, HIGH);
    digitalWrite(INIDICATE_COUNT, HIGH);
    digitalWrite(GPIO_NUM_2, HIGH);

    Serial.begin(115200);
    serialLS.begin(19200, SERIAL_8N1, RXLS, TXLS);
    serialHMI.begin(19200, SWSERIAL_8N1, RXDNEX, TXDNEX, false, 256);
    serialMB.begin(19200);

    hmi.echoEnabled(false);
    hmi.hmiCallBack(onHMIEvent);
    hmi("rest");

    Rtc.Begin();

#ifdef verAnalogInput
    ads.setGain(GAIN_ONE);
    ads.begin();
    lls_analog_u = new LS_ANALOG_U(ads, 2);
    lls_analog_f = new LS_ANALOG_F(IN_ANALOG_F);
#endif

    flash.begin("eerom", false);
    int k = flash.getInt("impulse_count", 1680); // чтение из eerom значения K счетчика
    countV = new COUNTER(k);

    lls_Empty = new LS_EMPTY();
    lls = lls_Empty;

    tank = new TANK(countV);
    tar = new TARRING(countV, tank);
    pump = new Out(OUT_PUMP);

    lls_RS485 = new LS_RS485(&serialLS, 1);
    lls_Ble = new LS_BLE();
    lls_Ble->echoEnabled(false);

    pinMode(IN_KCOUNT, INPUT_PULLUP);           // инициализация входа импульсов ДАРТ
    attachInterrupt(IN_KCOUNT, rpmFun, CHANGE); // функция прерывания

    configureModbusTable();

#ifdef verATP
    lls_ATP = new LS_RS485(&serialLS, 100);
#endif

    // // страница  списка файлов
    // server.on("/", HTTP_GET, [](AsyncWebServerRequest *request)
    //           { request->send(200, "text/html", "<p>ATS 2023</p><p>" + String(__DATE__) + "</p><p>" + listDir(SPIFFS, "/", 0) + "</p>"); });

    // // скачивание лог-файла
    // server.on("/log.csv", HTTP_GET, [file = "/log.csv"](AsyncWebServerRequest *request)
    //           { getDataLog(request, file); });

    // // удаление файла логов
    // server.on("/delete", [](AsyncWebServerRequest *request)
    //           { request->send(200, "text/html", "<p>ATS - delete log file</p>" + deleteLog()); });

#ifdef ENABLE_WEB_PORTAL
    wifiInit();
#endif

    if (!LittleFS.begin())
        Serial.println("FS Error");

    log_e("Ver: %s", VER);

#ifdef ENABLE_WEB_PORTAL
    ui.attachBuild(buildPage);
    ui.attach(actionDownload);
    ui.attach(actionPage);
    ui.start("ATS");
    ui.downloadAuto(0); // отключить авто скачивание
    ui.enableOTA();
#endif

    xTaskCreatePinnedToCore(
        calculate_speedPump,        /* Вычисление скорости потока */
        "Task_calculate_speedPump", /* Название задачи */
        4096,                       /* Размер стека задачи */
        NULL,                       /* Параметр задачи */
        1,                          /* Приоритет задачи */
        NULL,                       /* Идентификатор задачи, чтобы ее можно было отслеживать */
        1);                         /* Ядро для выполнения задачи (0) */

    xTaskCreatePinnedToCore(
        updateLS,        /* */
        "Task_updateLS", /* Обновление данных от ДУТ */
        16364,           /* Размер стека задачи */
        NULL,            /* Параметр задачи */
        1,               /* Приоритет задачи */
        NULL,            /* Идентификатор задачи, чтобы ее можно было отслеживать */
        0);              /* Ядро для выполнения задачи (0) */

#ifdef PRINTDEBUG
    xTaskCreatePinnedToCore(
        printDebugLog,        /*  */
        "Task_printDebugLog", /* Печать отладочной информации*/
        4096,                 /* Размер стека задачи */
        NULL,                 /* Параметр задачи */
        3,                    /* Приоритет задачи */
        NULL,                 /* Идентификатор задачи, чтобы ее можно было отслеживать */
        tskNO_AFFINITY);      /* Ядро для выполнения задачи (0) */
#endif

    xTaskCreatePinnedToCore(
        sendNextion,        /* обновление данных HMI */
        "Task_sendNextion", /* Название задачи */
        8192,               /* Размер стека задачи */
        NULL,               /* Параметр задачи */
        4,                  /* Приоритет задачи */
        NULL,               /* Идентификатор задачи, чтобы ее можно было отслеживать */
        1);

    xTaskCreatePinnedToCore(
        readNextion,        /* чтение данных от HMI */
        "Task_readNextion", /* Название задачи */
        8192,               /* Размер стека задачи */
        NULL,               /* Параметр задачи */
        5,                  /* Приоритет задачи */
        NULL,               /* Идентификатор задачи, чтобы ее можно было отслеживать */
        1);

    datemod.controlFlowrate = true;
    datemod.mode = MENU;

    // индикация окончания загрузки
    digitalWrite(INDI_F_PIN_, LOW);
    digitalWrite(INIDICATE_COUNT, LOW);
    digitalWrite(GPIO_NUM_2, LOW);

    // таймер для светодиода индикации счетчика
    setupCountIndicatorTimer();
}

void loop()
{
    errors();
    updateModbusRegisters();
    hmi.listen();
#ifdef ENABLE_WEB_PORTAL
    ui.tick();
#endif

    switch (datemod.mode)
    {
    case MENU:
        modeMenu();
        break;
    case PUMPINGAUTO:
        modePumpAuto();
        break;
    case PAUSE:;
    case TAR:
        modeTarring();
        break;
    case PUMPINGOUT:
        modePumpOut();
        break;
    case END_TAR:
        exitTarring();
        break;
    case MESSAGE:
        stopPump();
        break;
    case SEARCH_BLE:
        break;
    }

    if (lls->getType() == ILEVEL_SENSOR::ANALOGE_F)
        digitalWrite(INDI_F_PIN_, HIGH);
    else
        digitalWrite(INDI_F_PIN_, LOW);
}

// void test()
// {
//   if (pump->get() == ON)
//   {
//     rpmFun();
//   }
// }

/*  ---------- Режим Меню ---------- */
void modeMenu()
{
    tar->reset();
    pump->off();
    datemod.id1 = 0;
    datemod.id2 = 0;
    counter_display_resetring = 0;
    autostop = false;
    flag_conect_ok = true;
}

/*  ---------- Режим Автоматическая выдача топлива ---------- */
void modePumpOut()
{
    if (tar->getVTank() <= tar->getVfuel())
        pump->off();
}

/*  ---------- Режим Тарировка ---------- */
void modeTarring()
{
    if (tar->getCountReffil() == 0)
    {
        if (tar->getVTank() > 200 && tar->getNumRefill() > 4)
            tar->saveResultRefuil(lls);
        else
            hmi("page menu"); //   возврат в меню при некорректных данных
    }

    if (tar->getVTank() <= tar->getVfuel()) // условие окончания тарировки
        endTarring();

    if (tar->getVTankRefill() * tar->getCountReffil() <= tar->getVfuel() && tar->getCountReffil() != tar->getNumRefill()) // условие окончания очередного пролива
        endRefill();
}

/*  ---------- Режим Автоматическое выкачивание ---------- */
void modePumpAuto()
{
    if (millis() - worktime > 30000)
    {
        if (pump->get() == ON && countV->getFlowRate() < 5) // скорость потока менее 5 л/мин
            pump->off();
    }
    if (pump->get() == OFF)
        worktime = millis();
}

/*  ---------- Продолжение тарировки  ---------- */
void proceedTarring()
{
    tar->saveResultRefuil(lls); // запись результата пролива
    errors();
    if (datemod.error == 32)
        return;
    autostop = false;
    time_start_refill = millis();
    datemod.mode = TAR;
    pump->on();
}

/*  ---------- Окончание очередного пролива  ---------- */
void endRefill()
{
    stopPump();
    if (datemod.mode == TAR && autostop == false)
    {
        autostop = true;
        start_pause = millis();
        datemod.mode = PAUSE;
    }

    if (millis() - start_pause < 5000)
        return;

    if (countV->getFlowRate() > 0) // проверка, что топливо больше не поступает в бак
    {
        delay(100);
        return;
    }

    if (tar->getTimePause() == 0) // пауза если ДУТ цифровой
        digitalpause();
    else if (millis() - start_pause > tar->getTimePause() * 60000) // пауза если ДУТ аналоговый
        proceedTarring();
}

/*  ---------- Финал тарировки  ---------- */
void endTarring()
{
    autostop = true;
    stopPump();

    while (countV->getFlowRate() > 0) // проверка, что топливо больше не поступает в бак
        delay(1000);
    exitTarring();
}

/*  ---------- Выход из тарировки  ---------- */
void exitTarring()
{
    if (datemod.mode != END_TAR)
    {
        datemod.mode = END_TAR;
        if (tar->getTimePause() == 0)
            if (lls->getVecLevel()->size() == 0)
            {
                delay(100);
                return;
            }
        // start_pause = millis() + TIME_PAUSE_END_TAR / 4;
        tar->saveResultRefuil(lls);
    }
    // if (start_pause - millis() > 50)
    //     return;
    hmi("page t_end");
    // delay(200);
    datemod.mode = END_TAR_HMI;
}

/*  ---------- Считывание данных с ДУТ  ---------- */
void updateLS(void *pvParameters)
{
    for (;;)
    {
#ifdef verATP
        if (datemod.mode == MENU)
            lls_ATP->update();
#endif
        if (datemod.mode == TAR || datemod.mode == PAUSE || datemod.mode == COUNT)
            if (lls->getType() != ILEVEL_SENSOR::NO_LLS)
            {
                lls->update();
                // test();
                digitalWrite(GPIO_NUM_2, ON);
                delay(10);
                digitalWrite(GPIO_NUM_2, OFF);
            }

        vTaskDelay(pdMS_TO_TICKS(TIME_UPDATE_LLS));
    }
    vTaskDelete(NULL);
}

/*  ---------- Считывание данных с ДУТ  ---------- */
void updateLS()
{
#ifdef verATP
    if (datemod.mode == MENU)
        lls_ATP->update();
#endif

    if (datemod.mode == TAR || datemod.mode == PAUSE || datemod.mode == COUNT)
        if (lls->getType() != ILEVEL_SENSOR::NO_LLS)
        {
            lls->update();
            // test();
        }
}

/*  ---------- Вычисление скорости потока  ---------- */
void calculate_speedPump(void *pvParameters)
{
    for (;;)
    {
        countV->updateFlowRate();
        vTaskDelay(pdMS_TO_TICKS(TIME_UPDATE_SPEED_PUMP));
    }
    vTaskDelete(NULL);
}

/*  ---------- Ошибки ДУТ  ---------- */
void errors()
{
    int error = 0;
    if (datemod.mode == MESSAGE || datemod.mode == END_TAR || datemod.mode == CALIBR || datemod.mode == MENU)
        return;

    if (lls->getType() != ILEVEL_SENSOR::NO_LLS) // если ДУТ подключен
    {
        if (datemod.mode == SEARCH_BLE) // ДУТ BLE и режим поиск
            return;

        // if (tar->getType() == tarring::AUTO) //  если тарировка в автоматическом режиме
        if (tar->getTimePause() == 0)
        {
            error = lls->getError(); // чтение ошибок ДУТ

            if (datemod.mode == TAR)
                if (tar->getCountReffil() > 2) // проверка увеличения данных с ДУТа в проливах
                    if (tar->getNRefill(tar->getCountReffil() - 1) < 10 + tar->getNRefill(tar->getCountReffil() - 2))
                        error |= 1 << 5;

            if (datemod.mode == SETTING) // проверка, что тарировка начинается с приемлемого уровня ДУТ
                if (lls->getLevel() > lls->getLevelStart())
                    error |= 1 << 7;
        }
    }

    // проверка, что 30 секунд скорость пролива меньше 2л/мин
    if (datemod.controlFlowrate)
    {
        if (pump->get() == ON)
        {
            if (countV->getFlowRate() < 2)
            {
                if (millis() > pump->getTimeStart() + 30000)
                    error |= 1 << 6;
            }
            else
                pump->setTimeStart();
        }
    }
    if (error)
    {
        // Serial.printf("\nErr: %d", error);
        if (datemod.mode != MESSAGE)
            hmi("page message");
        datemod.mode = MESSAGE;
        pump->off();
        datemod.error = error;
    }
}

/*  ---------- Функция подсчета импульсов с ДАРТ  ---------- */
void rpmFun()
{
    if (micros() - time_counter_imp > MIN_DURATION)
    {
        const unsigned long pulseCount = countV->setKcount();
        if (pulseCount % 20 == 0 && !isCountIndicatorTimerActive())
        { 
            // digitalWrite(INIDICATE_COUNT, !digitalRead(INIDICATE_COUNT));
            digitalWrite(INIDICATE_COUNT, HIGH);
            startCountIndicatorTimer();
        }
    }
    time_counter_imp = micros();
}

/*  ---------- Парсинг полученых данных от дисплея Nextion  ---------- */
void onHMIEvent(String messege, String data, String response)
{
    if (messege.isEmpty())
        return;

    switch (messege.toInt())
    {
    case 1:
        datemod.mode = MENU;
        break;
    case 2:
        datemod.mode = CALIBR;
        break;
    case 3:
        datemod.mode = COUNT;
        break;
    case 7:
        datemod.mode = SEARCH_BLE;
        break;
    case 8:
        if (!autostop)
            datemod.mode = TAR;
        else if (datemod.mode != END_TAR)
            datemod.mode = PAUSE;
        break;
    case 9:
        datemod.mode = PUMPINGAUTO;
        break;
    case 10:
        datemod.mode = PUMPINGOUT;
        break;
    case 11:
        datemod.mode = END_TAR_HMI;
        break;
    case 12:
        datemod.mode = MESSAGE;
        break;
    case 13:
        datemod.mode = SETTING;
        break;
    default:
        break;
    }

    /*  ----------  Экран Меню  ---------- */
    if (messege == "menu")
    {
        int k = flash.getInt("impulse_count", 1680); // чтение из eerom значения K счетчика
        countV->setKinLitr(k);
        datemod.error = 0;
        if (lls->getType() != ILEVEL_SENSOR::NO_LLS)
        {
            // сброс ДУТа BLE без номера и не найденного в поиске
            if (lls->getNameBLE() == "" || lls->getError() == ILEVEL_SENSOR::error::NOT_FOUND)
                delete_lls();
        }
    }

#ifdef verAnalogInput
    else if (messege == "au!")
    {
        lls = lls_analog_u;
        lls->search();
    }

    else if (messege == "ag!")
    {
        lls = lls_analog_f;
        digitalWrite(INDI_F_PIN_, HIGH);
        lls->search();
    }
#endif

    else if (messege == "rs485!")
    {
        lls = lls_RS485;
        if (lls->search())
            tar->setTimePause(0);
    }

    else if (messege == "ble!")
    {
        lls = lls_Ble;
        lls->newBLE("");
    }

    else if (messege == "no_lls!")
    {
        delete_lls();
    }

    else if (messege == "TD_") // получение имени ДУТа BLE Эскорт
    {
        lls->newBLE(messege + data);
        lls->search();
    }

    else if (messege == "pump")
    {
        pump->get() ? stopPump() : startPump();
    }

    else if (messege == "endtarr") // окончание тарировки
    {
        exitTarring();
    }

    else if (messege == "save") // сохранение тарировки
    {
        saveLog();
    }

    else if (messege == "resetring")
    {
        if (tar->getVfuel())
            tar->saveResultRefuil(lls);
        return;
    }
    else if (messege == "reset")
    {
        tar->reset();
        counter_display_resetring = -1;
    }

    else if (messege == "CALIBR")
    {
        data.toInt() ? countV->reset() : stopPump();
    }

    else if (messege == "k_count") // получение промежуточного значения k_in_Litr
    {
        countV->setKinLitrCalibr(data.toInt());
    }

    else if (messege == "save_k") // получение нового К, запись в память
    {
        flash.putInt("impulse_count", data.toInt()); // запись в eerom значения K счетчика
        countV->setKinLitr(data.toInt());
    }
    else if (messege == "id") // получение номера тарируемого объекта
    {
        tar->setId(data);
        tar->setTStart(Rtc.GetDateTime());
    }
    else if (messege == "vtank") // получение объема бака
    {
        tank->setVTank(data.toInt() * 10);
    }
    else if (messege == "qt") // получение количества проливов
    {
        tar->setNumRefill(data.toInt());
    }

    /*  ----------  Получениее времени  ---------- */
    if (messege == "date")
    {
        auto index_sym = data.indexOf(';');
        auto DATE = data.substring(0, index_sym);
        auto TIME = data.substring(index_sym + 1, data.length());
        // Serial.printf("Date %s Time %s\n", DATE, TIME);

        // Для установки  времени
        RtcDateTime compiled = RtcDateTime(DATE.c_str(), TIME.c_str());
        Rtc.SetDateTime(compiled);
    }

    if (messege == "pause")
    {
        if (data.toInt())
        {
            tar->setTimePause(data.toInt());
        }
        else
        {
            // tar->setType(tarring::AUTO);
            if (lls->getType() != ILEVEL_SENSOR::NO_LLS)
                tar->setTimePause(0);
            else
                hmi("select0.val", tar->getTimePause());
        }
    }

    if (messege == "clear_err")
    {
        // switch (datemod.error)
        // {
        // case ILEVEL_SENSOR::NOT_FOUND:
        //   datemod.mode = TAR;
        //   if (lls->getType() != ILEVEL_SENSOR::NO_LLS)
        //     if (lls->getType() == ILEVEL_SENSOR::RS485)
        //     {
        //       Serial.println("Дут RS485 не найден. Ищем...");
        //       lls->search();
        //     }
        //     if (lls->getType() == ILEVEL_SENSOR::BLE_ESKORT)
        //     {
        //       Serial.println("Дут BLE не найден. Ищем...");
        //       lls->search();
        //     }
        //   datemod.error = 0;
        //   autostop = false;
        //   break;
        // case ILEVEL_SENSOR::LOST:
        //   datemod.mode = TAR;
        //   if (lls->getType() != ILEVEL_SENSOR::NO_LLS)
        //     if (lls->getType() == ILEVEL_SENSOR::RS485)
        //     {
        //       Serial.println("Дут RS485 потерян. Ищем...");
        //       lls->searchLost();
        //     }
        //     if (lls->getType() == ILEVEL_SENSOR::BLE_ESKORT)
        //     {
        //       Serial.println("Дут BLE потерян. Ищем...");
        //       lls->search();
        //     }
        //   datemod.error = 0;
        //   autostop = false;
        //   break;

        // default:
        //   break;
        // }
        if (datemod.error == 32)
            tar->deleteResultRefuil(lls);

        datemod.error = 0;
        lls->clearError();
    }

    if (messege == "contrFlowrate")
    {
        if (data == "1")
            datemod.controlFlowrate = true;
        if (data == "0")
            datemod.controlFlowrate = false;
    }
}

/*  ---------- данные с Nextion ---------- */
void readNextion(void *pvParameters)
{
    for (;;)
    {
        hmi.listen();
        // vPrintString("readNextion");
        // vTaskDelayUntil(&xLastWakeTime, pdMS_TO_TICKS(TIME_UPDATE_HMI));
        vTaskDelay(pdMS_TO_TICKS(TIME_UPDATE_HMI));
    }
    vTaskDelete(NULL);
}
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

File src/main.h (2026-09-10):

#pragma once


// #define PRINTDEBUG
// #define verATP
#define verAnalogInput

#include <Arduino.h>
#include <esp_arduino_version.h>
#include <Wire.h>
#include <SPI.h>
// #include <AsyncTCP.h>
// #include <ESPAsyncWebServer.h>
// #include <AsyncElegantOTA.h>
#include <freertos/task.h>
#include <FreeRTOSConfig.h>
#include <SPIFFS.h>
// #include <SPIFFSEditor.h>
#include "Preferences.h"
#include <SoftwareSerial.h>
#include <RtcDS3231.h>
#ifdef ENABLE_WEB_PORTAL
#include <GyverPortal.h>
#endif

#ifdef verAnalogInput
#include <Adafruit_ADS1X15.h>
#include "LS_ANALOG_U.h"
#include "LS_ANALOG_F.h"
#endif
#include "COUNTER.h"
#include "TARRING.h"
#include "TANK.h"
#include "NEXTION.h"
#include "Out.h"
#include "LS_RS485.h"
#include "LS_BLE.h"
#include "LS_EMPTY.h"
#include "ModbusTable.h"

#define LittleFS SPIFFS

class LS_ANALOG_F;

#define serialLS Serial1
#define serialMB Serial2

extern const char *ssid;
extern const char *password;
extern const char *VER;

struct LoginPass
{
  char ssid[20];
  char pass[20];
};

extern LoginPass lp;

#define PLATE_v2 // PLATE_v1 - плата вер1,  PLATE_v2 - плата вер2 (2023)

// #ifdef PLATE_v1
// static const uint8_t INDI_F_PIN_ = GPIO_NUM_2;     // (2) индикатор включения частотного ДУТа
// static const uint8_t OUT_PUMP = GPIO_NUM_12;        // вывод управления насосом
// static const uint8_t INIDICATE_COUNT = GPIO_NUM_13; // вывод индикатора входных импульсов
// static const uint8_t IN_KCOUNT = GPIO_NUM_5;        // вход счетчика топлива
// static const uint8_t RXDNEX = GPIO_NUM_23;          //
// static const uint8_t TXDNEX = GPIO_NUM_19;          //
// static const uint8_t RXLS = GPIO_NUM_27;
// static const uint8_t TXLS = GPIO_NUM_14;
// #endif

#ifdef PLATE_v2
static const uint8_t INDI_F_PIN_ = GPIO_NUM_25;     // (25) индикатор включения частотного ДУТа
static const uint8_t IN_ANALOG_F = GPIO_NUM_34;     // вход частотного ДУТа
static const uint8_t OUT_PUMP = GPIO_NUM_12;        // вывод управления насосом
static const uint8_t INIDICATE_COUNT = GPIO_NUM_13; // вывод индикатора входных импульсов
static const uint8_t IN_KCOUNT = GPIO_NUM_5;        // вход счетчика топлива
static const uint8_t RXDNEX = GPIO_NUM_23;          //
static const uint8_t TXDNEX = GPIO_NUM_19;          //
static const uint8_t RXLS = GPIO_NUM_27;
static const uint8_t TXLS = GPIO_NUM_14;
#endif


// режимы работы
enum type
{
  CALIBR,      // Калибровка счетчика
  PUMPINGAUTO, // Откачка топлива автоматом
  TAR,         // Тарировка
  SETTING,     // Настройка тарировки
  MENU,        // Меню
  COUNT,       // Счетчик
  PUMPINGOUT,  // Выдача топлива
  END_TAR,
  END_TAR_HMI,
  MESSAGE,
  SEARCH_BLE,
  PAUSE,
  SET_DATE,
  SET_WEB
};

extern String errorStringWeb;                       //  строка ошибки
extern int counter_display_resetring;
extern volatile unsigned time_counter_imp;
const long MIN_DURATION = 500;
const uint16_t TIME_UPDATE_LLS = 10000;         // период обновления данных ДУТ
const uint16_t TIME_UPDATE_HMI = 300;           // период обновления данных на дисплее, мсек
const uint16_t TIME_UPDATE_SPEED_PUMP = 2000;   // период обновления скорости потока
const uint16_t TIME_PAUSE_END_TAR = 20000;      // пауза в конце тарировки для передаче данных в систему мониторинга

extern unsigned long start_pause, worktime, time_start_refill, time_LLS_update, time_stop_flow_rate;
extern bool autostop;
extern bool flag_HMI_send;
extern bool flag_conect_ok;                     // флаг удачного получения данных от ДУТ

#ifdef ENABLE_WEB_PORTAL
struct WebData {
  int w_vtank_pumpingout = 0;
};

extern WebData web_data;
#endif

extern const char *LOG_FILE_NAME;

void rpmFun();
void modeMenu();
void modePumpOut();
void modeTarring();
void modePumpAuto();
void endTarring();
void endRefill();
void proceedTarring();
void errors();
void digitalpause();
void startPump();
void stopPump();
String makeLlsDateToDisplay(ILEVEL_SENSOR *_lls);
void onHMIEvent(String messege, String data, String response);
void exitTarring();
String saveLog();

void delete_lls();
String saveLog();
String deleteLog();

String listDir(fs::FS &fs, const char *dirname, uint8_t levels);

void updateLS(void *pvParameters);
void updateLS();
void readNextion(void *pvParameters);
void calculate_speedPump(void *pvParameters);
void onHMIEvent(String messege, String data, String response);
#ifdef PRINTDEBUG
void printDebugLog(void *pvParameters);
#endif

extern hw_timer_t *My_timer;
void IRAM_ATTR onTimer();

extern RtcDS3231<TwoWire> Rtc;

extern Preferences flash;
extern EspSoftwareSerial::UART serialHMI;

#ifdef ENABLE_WEB_PORTAL
extern GyverPortal ui;
#endif

// ДУТ
extern ILEVEL_SENSOR *lls;
extern LS_RS485 *lls_RS485;
extern LS_BLE *lls_Ble;
extern LS_EMPTY *lls_Empty;
#ifdef verAnalogInput
extern Adafruit_ADS1115 ads; /* Use this for the 16-bit version */
extern LS_ANALOG_F *lls_analog_f;
extern LS_ANALOG_U *lls_analog_u;
#endif

#ifdef verATP
// ДУТ в емкости АТП
extern LS_RS485 *lls_ATP;
#endif

// насос
extern Out *pump;
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

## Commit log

2025-10-10 Автоматическая тарировочная станция 2025 ver3.0 web 2.0
    [ATC ver_2022.drl, ATC ver_2022_copper_bottom.gbr, ATC ver_2022_copper_top.gbr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]
2025-11-04 Изменение readme и индикации поступления импульсов счетчика
